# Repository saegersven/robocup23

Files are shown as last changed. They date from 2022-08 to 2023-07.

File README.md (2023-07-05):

# Robocup Junior Rescue Line 2023
### Team BitFlip

* [Youtube Channel](https://www.youtube.com/@evbrobocup)
* [Website](http://kraemer123.de/)
* [2022 Repository](https://github.com/saegersven/robocup)

### <u>Our ToDo List:</u>

#### Software
- [ ] ignore silver for 1s after ramp to get rid of false positives when driving down seesaw/ramp
- [ ] LoPs in rescue area not working
- [ ] check_silver after restart not working, cam servo does not tilt upwards
- [ ] after green dot: check left/right like in Kassel
- [ ] exit
- [ ] investigate: why is cam servo not ALWAYS attached. Sometimes its detached
- [ ] investigate why cam servo sometimes turns when stop.py is being called from run.sh
- [ ] reduce sensitivity when few black pixels (gaps)

#### CAD

#### 3D Printing

### Problems based on runs in St Augustin (descending order of importance, will probably never be implemented)
- [ ] increase motor speed when frame is the same of long time (indicating the robot got stuck)
- [ ] turn lineangle before gap? Maybe drive backwards a few times to allow for slight corrections
- [ ] missed black line during obstacle
- [ ] corner approach: check contour to avoid false positives
- [ ] intersection: confused right with left turn (vid 4, 1:45)
- [ ] obstacle: line after obstacle pls fix
- [ ] prefer living victims when when !ignore_dead 
- [ ] find exit
- [ ] random thread(?) stop during rescue. Maybe add pull down resistor or check for press  duration
- [ ] more labeled victim data to avoid losing victim during search
- [ ] more ml data with multiple victim overlapping (and far away)
- [ ] beginning of victim search: why frame lost?
- [ ] ignore upper frame area when looking for victims
- [ ] find corner more precise (more ml data of corners far away)
- [ ] reajust robot position relative to corner when driving towards it
- [ ] investigate: vid 4, 3:05 random thread crash
- [ ] turn line angle before obstacle
- [ ] check if victim has been rescued successfully (look at black corner)
- [ ] rescue kit: close gripper while driving forward 
- [X] rewrite find_center using VL53L0X and Gyro
- [X] VL53L0X instead of HCSR04
- [X] Gyro sensor (turning, ramps up and down, adjust speed accordingly)
- [X] intersection: turn 60 degs with gyro and rest with camera until line angle = 0
- [X] oscillating during linefollowing (even when following straight lines)
- [X] drive towards rescue kit so its always in the same y position (not only x) to facilitate pickup

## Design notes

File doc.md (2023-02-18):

# Software

Our robot has two programs: The main program runs on a Raspberry Pi 4B+, and is written in C++ with OpenCV and tensorflow as the main dependencies. The secondary program runs on a Teensy 3.6, that acts as a motor controller and receives commands from the main program.

The main program follows the line, navigates intersections, detects obstacles, picks up the rescue kit and rescues the victims using mostly a single Raspberry Pi Camera v2.1 mounted high up at the front of the robot. It is mounted on a servo so it can be rotated upwards to look for victims. During line following, it looks almost straight down.

The main program is written in C++ instead of Python because we perform custom operations on individual pixels, which can't be easily done in Python without significantly sacrificing performance.

## Line following

The main library we use for our Computer Vision tasks is OpenCV. We grab frames from the camera using the library's `cv::VideoCapture` class. We get a `cv::Mat` object which contains a single image. The camera captures in a very low resolution of 80x48 pixels, which combined with optimized algorithms allows the robot to adjust its motor speeds about 100 times per second.

During line following, a frame might look like this:

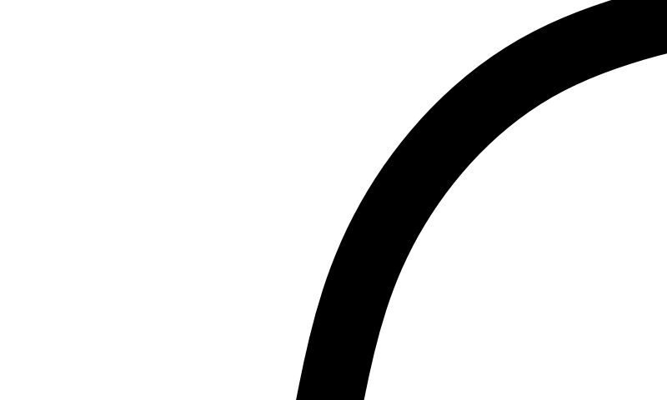
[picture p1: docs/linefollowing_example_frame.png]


Now we use a simple binary thresholding operation to find every black pixel. We now iterate over each of the black pixels and calculate the angle from the bottom center of the image to the pixel:

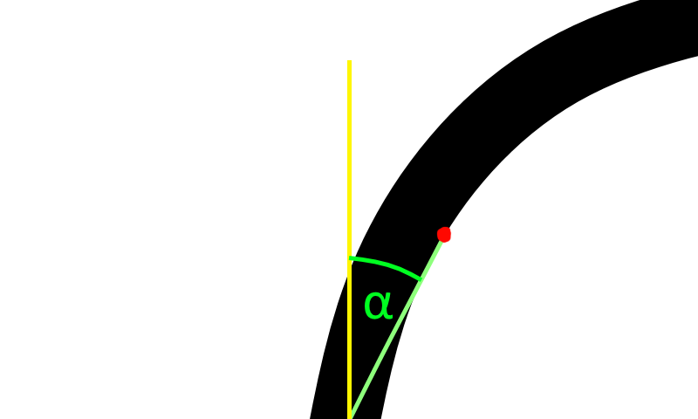
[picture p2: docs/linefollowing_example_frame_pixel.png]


This angle is weighed according to its distance from the bottom center since we don't want pixels near the bottom center to contribute as much to the line angle. Pixels very far away also have lower weights. The pixels are also weighed according to how close their angle is to the angle of the last line. This prevents the robot from following the wrong lines and also helps it navigate T-shaped intersections. The weights are calculated when starting the program and saved in maps for quick access. We now use a weighted average of all the angles of the black pixels to obtain the line angle, which might look like this:

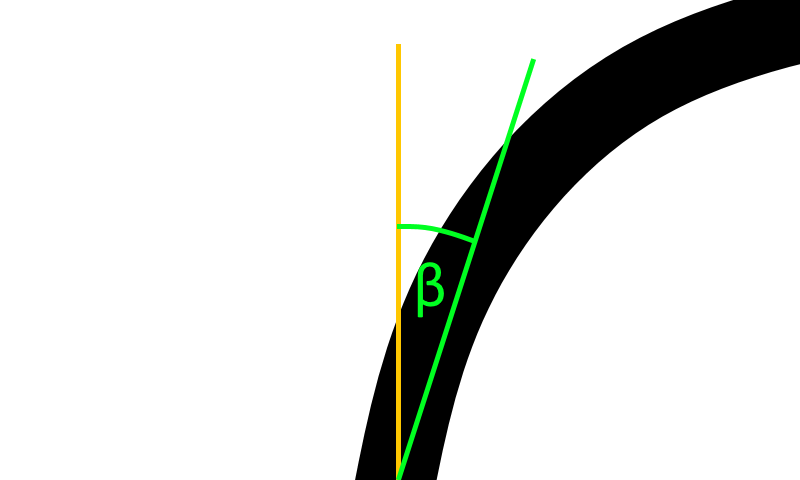
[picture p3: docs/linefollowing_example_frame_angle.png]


This angle is then multiplied by a sensitivity factor and simply added or subtracted from the motor speeds. There is no need for integration or differentiation. This algorithm, combined with a center of rotation of the robot around the front axis, allows the robot to follow even complicated lines very quickly.

### Intersections

During line following, the frame is continuously sampled for green pixels by calculating the ratio of the green component of a pixel to the sum of the blue and red. If there are enough green pixels in the frame, we find contours using a simple recursive algorithm. Contours which are too small are discarded. The only contours that remain are green points.

Now we cut out a square part of the image around the green points and use the binary image from before to iterate over all the black pixels in that cutout. We calculate the average of all the black pixels (depicted below in blue). Now the quadrant of the average black pixel tells us where the robot needs to go. This has proven to be a very simple and robust algorithm.

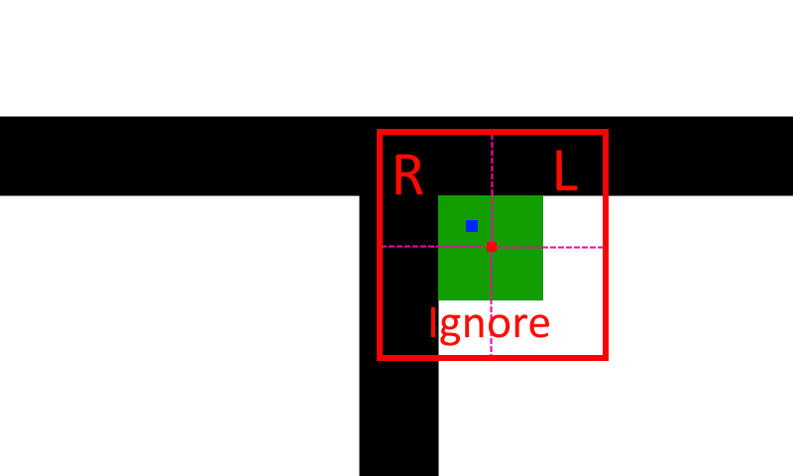
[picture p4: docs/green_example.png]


### Rescue kit

Similarly to the intersection algorithm, we continuously look for blue pixels using the same metric as for green. When we find a contour that is big enough, we calculate the angle from the bottom center to that contour, turn in that direction, pick the rescue kit up and return to following the line.

### Detecting the entrance to the evacuation zone

Detecting a reflecting strip of tape is surprisingly difficult using just a camera. We have tried different algorithms in the past, such as comparing the image to a pre-saved image of the tape, and detecting the reflection of red LEDs mounted near the camera. We now use a small machine learning model trained in Keras/Tensorflow on a few thousand images, which runs simultaneously in a separate thread.

## Evacuation zone

### Strategy

TODO

### Detecting victims

Similarly to the reflective tape at the entrance, two of the victims are reflective as well. This fact as well as debris scattered around the evacuation zone make it difficult to use traditional circle-detection algorithms such as Hough transforms to detect victims. At least we never got it to work reliably. Instead, we are using a machine learning model trained on thousands of images. We have labelled them in Microsoft VoTT. The bounding boxes are assigned one of two tags: "living" or "dead". The neural network is similar to the popular "Yolo" architecture for object detection, but it is greatly simplified.

The image is divided up chunks. For each chunk we want to know if there is a living or a dead victim, or none. This means that the neural net has to essentially output an image with two channels, containing probabilities. Below you can see an input image with 5x4 chunks and two numbers in each chunk, which are probabilities for our two classes "living" and "dead".

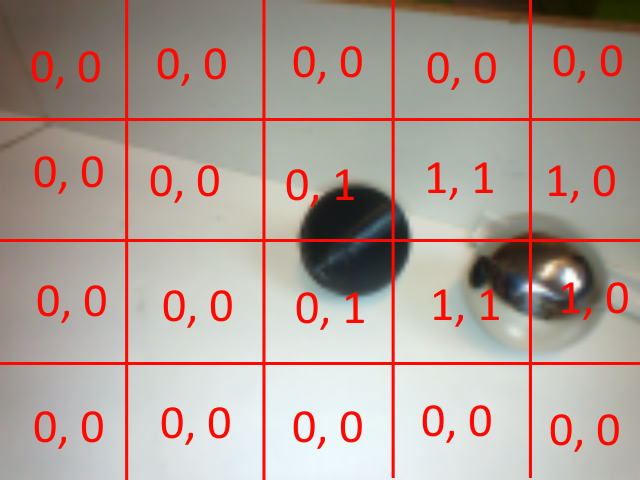
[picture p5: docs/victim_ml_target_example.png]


5x4 chunks is of course not fine enough to pick up victims accurately. We use 32x20 chunks in our model. When visualizing the target images, dead victims appear blue, and living victims green.

The model is created in Python using Keras' `Sequential` class as follows:

```python
model = Sequential([
    layers.Rescaling(1./255, input_shape=(input_height, input_width, 1)),
    layers.Conv2D(8, 5, padding='same', activation='relu'),
    layers.MaxPooling2D(8),
    layers.Conv2D(16, 3, padding='same', activation='relu'),
    layers.Dropout(0.1),
    layers.Flatten(),
    layers.Dense(Ys * Xs * Cs, activation='linear'),
    layers.Reshape((Ys, Xs, Cs))
])
```

Below you can see two training images and their respective targets (left) and two test images on unknown data with output (right).

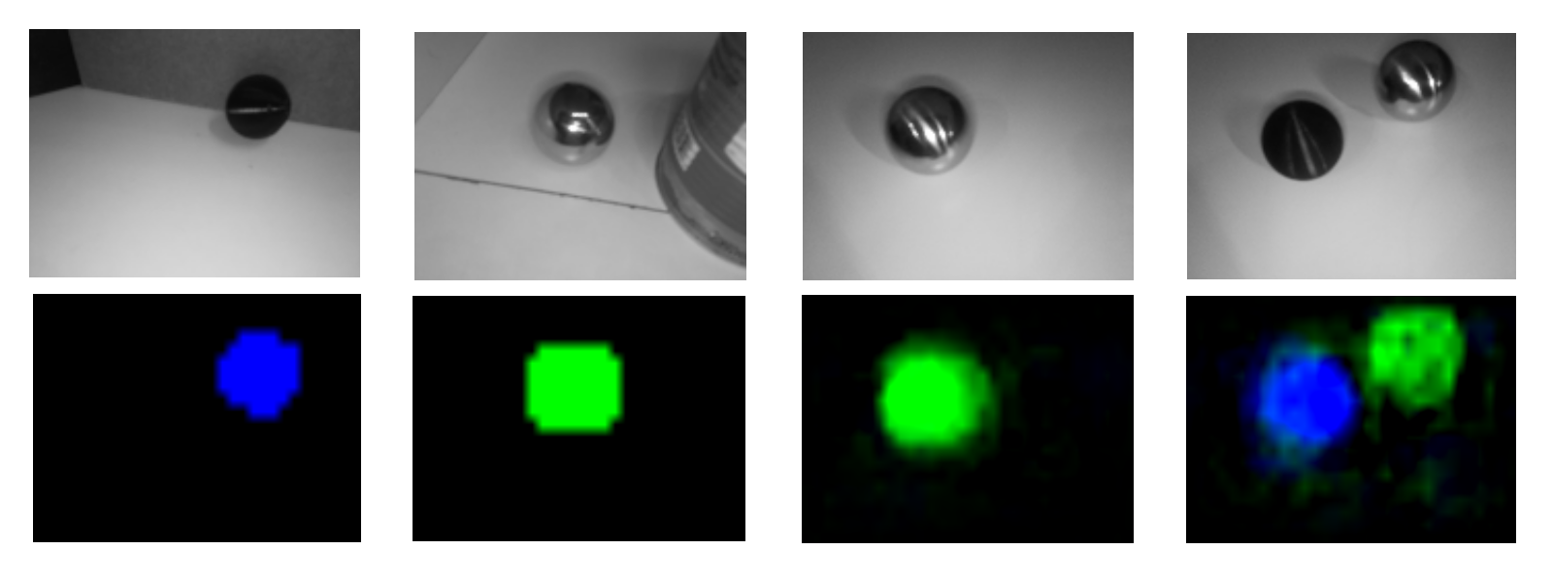
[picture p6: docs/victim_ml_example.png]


Now we just need to extract the victim positions from the output using simple thresholding operations and contour finding. The neural net runs at about 5 fps on the Raspberry Pi and detects victims accurately with almost no false-positives.

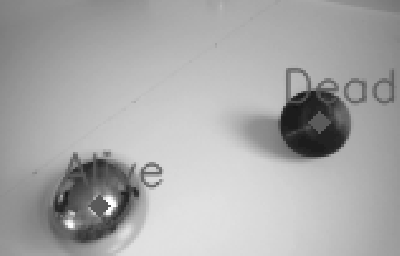
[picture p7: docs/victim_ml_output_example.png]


# Hardware and low-level software

## RasPi <-> Teensy protocol

Communication is via I2C. The Teensy is the secondary device (Address 0x2a) and acts as a motor controller.

| Command | ID | Data | Data type[s] | Description |
| - | - | - | - | - |
| Motor | 11 | Motor speeds | int8[2] | Sets front motor speeds. Rear motor speeds are set automatically |
| Stop | 21 | - | - | Stops all four drive motors |
| Servo | 31 | Servo ID and angle | uint8[2] | Move servo to angle |
| Ready | 41 | - | - | Notify Teensy that the main program is ready to be started |
| Home Servos | 51 | - | - | Set Servos to home positions when resetting the robot |
| Arm Down | 61 | - | - | Move arm down |
| Arm up | 71 | - | - | Move arm up |
| Unload | 91 | - | - | Unload victims and rescue kit |
| Pick up | 101 | - | - | Pick victim up |

Command IDs are non-sequential because communication is very noisy for some reason.

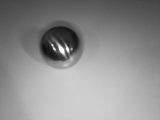
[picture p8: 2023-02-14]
docs/victim_ml_input.png

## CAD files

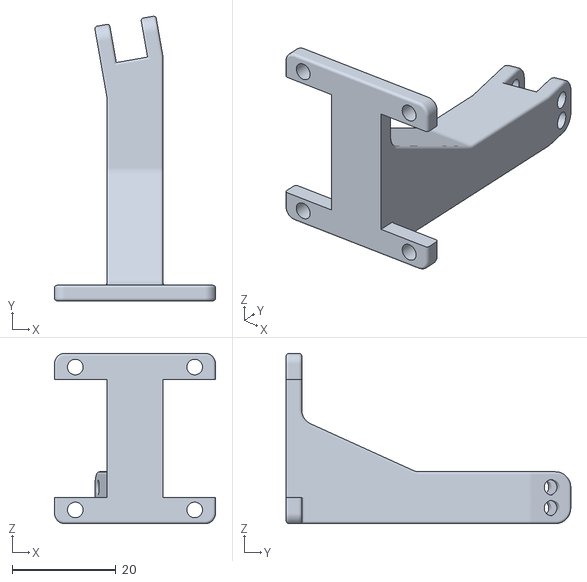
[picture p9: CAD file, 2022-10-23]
files/3D/Greifer_Basis.stl
31.0 x 54.8 x 32.8

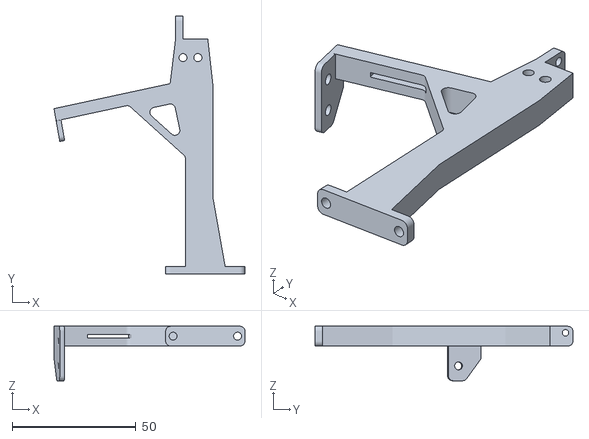
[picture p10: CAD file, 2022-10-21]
files/3D/Camera_Mount.stl
77.0 x 104.0 x 22.0

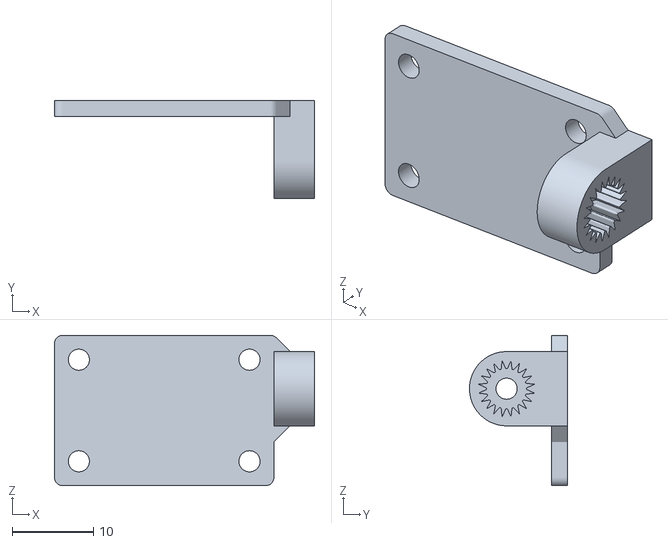
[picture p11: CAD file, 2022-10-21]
files/3D/Camera_Holder.stl
32.0 x 12.1 x 18.5

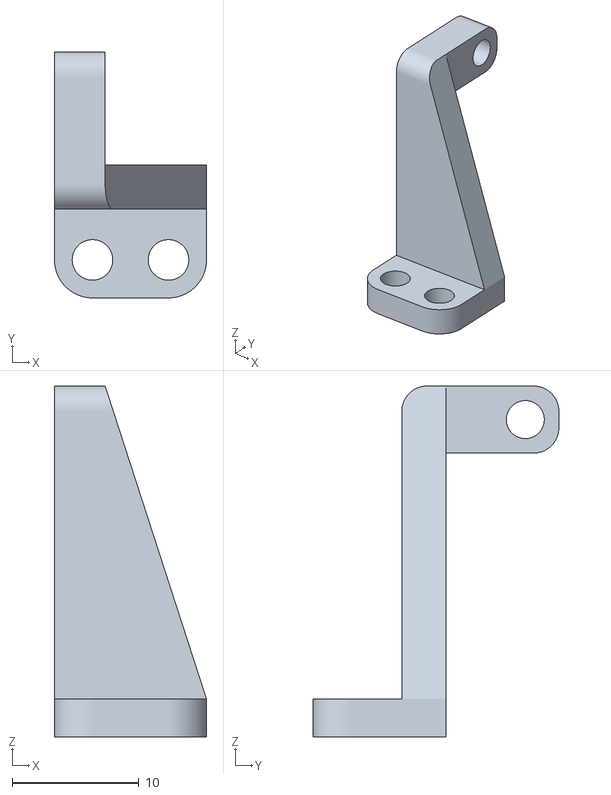
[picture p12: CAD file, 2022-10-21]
files/3D/Camera_Servo_Mount.stl
12.0 x 19.4 x 27.7

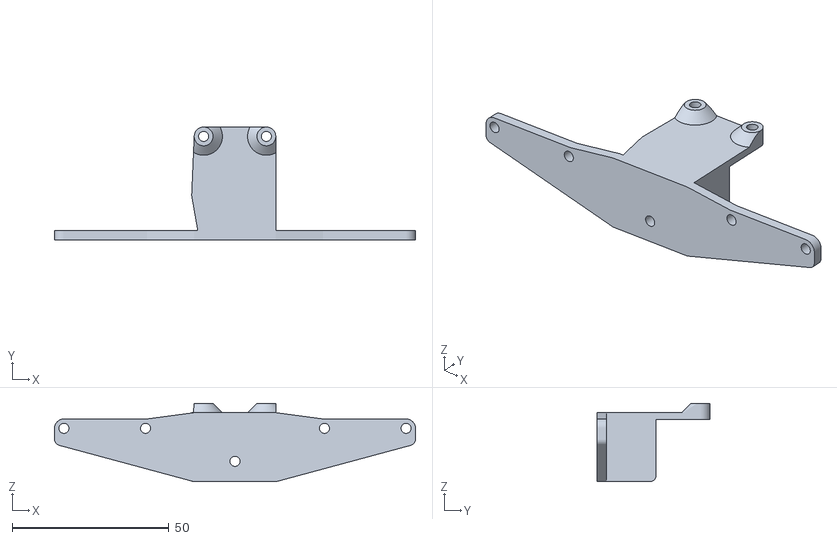
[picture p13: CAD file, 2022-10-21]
files/3D/Front_Mount.stl
115.0 x 36.0 x 25.0

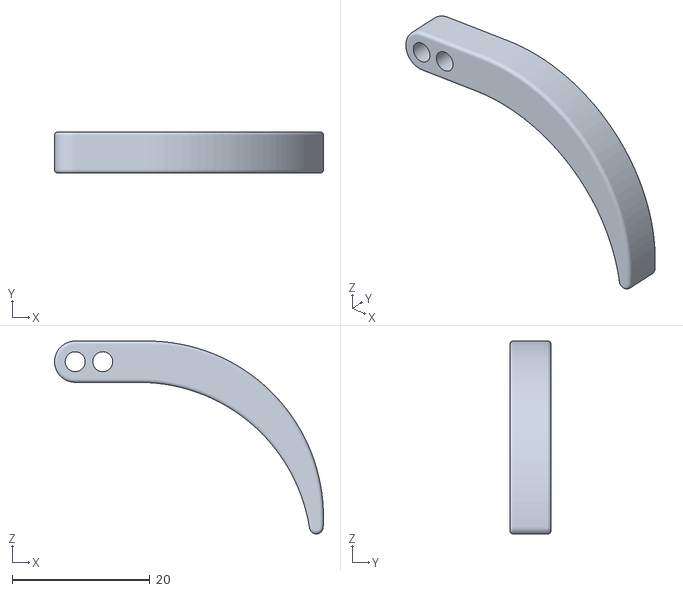
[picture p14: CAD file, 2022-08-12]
files/3D/Greifer_Arm.stl
39.0 x 6.00 x 28.0

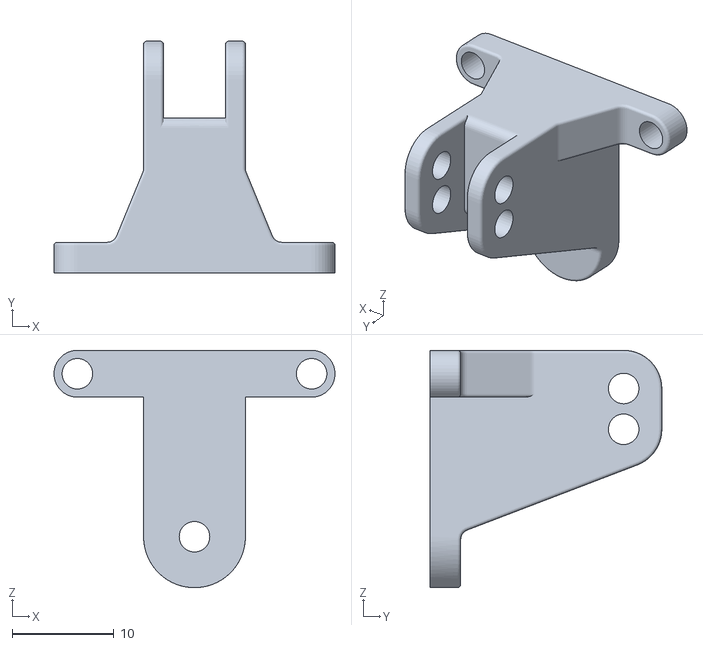
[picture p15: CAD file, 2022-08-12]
files/3D/Greifer_A.stl
27.6 x 22.8 x 23.3

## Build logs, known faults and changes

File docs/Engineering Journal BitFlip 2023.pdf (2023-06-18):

ROBOCUPJUNIOR RESCUE LINE 2023

ENGINEERING JOURNAL

## Team BitFlip

Abstract
This document is mainly about our development process and how we divided the work within our team. Through past RoboCup Junior participations, we gained plenty of experience on how to collaborate efficiently within a team, mainly due to trial and error and constant documenting on what we can improve.
Despite the abstract you are currently reading, this document mainly features a table where we tracked our development process over the past months. To facilitate collaboration, we shared this document through Google Docs with all team members and used a color code to identify areas of responsibility between all team members. The color code is as follows:

Sven Saeger
Jan-Niklas
Lukas
Whole Team

Furthermore, we met on a regular basis, mostly through video calls, however we also made use of GitHub and Trello to manage our todos.

Date | Agenda | Progress/Status | Next steps
July 2022 | | - Selected four 12V DC motors (Pololu 20D) - Researched various servo options and decided to use two servos for arm control and container gate control - Bought according servos - Designed and 3D-printed mounts for the servos and motors | - Complete the design of the robot chassis - Research suitable power source options
Aug ust 2022 | | | | - Assembled chassis with servos and motors - tested various | - Find suitable distance sensor - start PCB design
- Define project requirements and
specifications (new rules?!)
- Research and select components for the robot (mainly actuators)
- Begin designing the robot chassis
- Buy essential parts
- Research: which PCB software is best?
- Test different power source options
- Which sensors are needed?

- Which Microcontroller? | power source options, including: power banks, 2x 18650 and 2S Lipo cells
- Research about
| distance sensors
Sept emb er 2022 | - finished PCB prototype - integration tested motors with chassis and PCB | - start actual PCB design - design
Octo ber 2022 | - finished schematic - tested chassis + motors (ramps, seesaws, speed bumps, debris, point of rotation) | - start PCB routing - research: design architecture for main program
Nov emb er 2022 | - routed and ordered PCB (jlcPCB) - created repo | - test and assemble PCB ASAP - finish hardware (design and print remaining sensor mounts)
Dez emb er 2022 | - soldered and tested PCB - printed and mounted last 3d printed parts | - test robot as a whole (PCB, chassis) - software prototyping
Janu ary 2023 | - wrote and tested linefollowing - tested NN approach for intersections, worked not as well as our algorithm from last year | - improve intersections (use gyroscope to turn, align to intersection before turning) - rescue area - obstacle
Febr uary 2023 | - linefollowing done - worked on silver detection using tensorflow library - bought replacement Raspberry Pi, Teensy Microcontroller, Step up/down modules and motors | - finish rescue area - verify victim NN performance “in the real world” - test under competition conditions
- Intensive integration testing of motors and power supply
- PCB prototyping using perfboard
- create EasyEDA account
- start PCB schematic
- finish PCB
- order PCB
- Research: fast, but affordable PCB manufacturer
- write main routines and functions
- create new github repo
- integration test PCB
- finish hardware
- write linefollowing routine
- test linefollower
- order replacement parts
- finish rescue area
- create ml data for victims
- label ml data
- train victim NN, research about cloud computing
- train silver NN
- finish and test obstacle
- improve intersections (use gyroscope to turn, align to intersection before turning)

| - trained victim NN using google collab to facilitate collaboration within the team
Marc h 2023 | | - wrote packing list - all tests successful | - program exit (after evacuation zone)
- write packing list for German
Opens
- last tests

April
2023
- German Opens | - German Opens | - redesign gripper to use DC motor instead of servo (should work more reliable)
- increase
| | linefollowing speed
- redesign PCB
| | using better step up/down modules and Arduino Nano instead of Teensy as its easier to buy nowadays and more reliable
- decrease overall
| | chassis size
May 2023 | - redesigned gripper to use DC motor - new PCB design - designed new, smaller chassis | - update old 3d files - assemble PCB - test PCB - complete hardware of robot
June 2023 | - finished PCB - redesigned and printed mounts for camera and VL53L0X distance sensors - redesigned and printed BNO055 mount - redesigned victim container - competition simulation - booked hotel - registered team and mentor | - write “packing list” for World Cup - print replacement parts
- redesign gripper to use DC motor
instead of servo (should work more
reliable)
- increase linefollowing speed
- redesign PCB using better step up/down modules and Arduino Nano instead of Teensy as its easier to buy nowadays and more reliable
- decrease overall chassis size
- design new mounts etc due to new chassis
- solder PCB
- intensive testing
- create more ml data for victims
- label new data
- train new model
- World Cup registration and hotel booking
- create Poster about robot
- write TDP

- wrote TDP
- created and
printed poster

Appendix
For further information about our development process, please do not hesitate to check out our GitHub repository:

https://github.com/saegersven/robocup23

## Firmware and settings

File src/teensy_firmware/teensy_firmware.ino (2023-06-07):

#include <Servo.h>
#include <SPI.h>

#include "defines.h"

Servo servo_cam;
Servo servo_arm;
Servo servo_gripper1;
Servo servo_gripper2;
Servo servo_gate;


// GLOBAL VARIABLES
uint8_t buffer[128]; // stores received spi data
uint8_t num_bits = 0; // number of received bits

const Servo servos[5] = {
  servo_cam,
  servo_arm,
  servo_gripper1,
  servo_gripper2,
  servo_gate
};

const int servo_pins[5] = {
  SERVO_CAM_PIN,
  SERVO_ARM_PIN,
  SERVO_GRIPPER1_PIN,
  SERVO_GRIPPER2_PIN,
  SERVO_GATE_PIN
};

#define DEBUG 1
// only print when in debug mode:
#if DEBUG == 1
#define debug(x) Serial.print(x)
#define debugln(x) Serial.println(x)
#else
#define debug(x)
#define debugln(x)
#endif

void setup() {
  init();
}

// interrupt is called on rising spi clock
void sck_rising_interrupt() {
  buffer[num_bits / 8] |= digitalRead(MOSI_PIN) << (7 - num_bits % 8); // write received data to buffer
  ++num_bits;
}

float minvol = 10.0;
void loop() {
  while (digitalRead(CS_PIN) != LOW);
  while (digitalRead(CS_PIN) == LOW);
  int len = num_bits / 8;
  num_bits = 0;

  int cmd = (int)buffer[0]; // received command

  if (cmd == CMD_MOTOR) {
    // [CMD_MOTOR, left, right]
    int8_t left = (int8_t)buffer[1];
    int8_t right = (int8_t)buffer[2];

    m(left, right, 0);

    debug("M: ");
    debug(left);
    debug(" ");
    debugln(right);
  } else if (cmd == CMD_STOP) {
    stop();
  } else if (cmd == CMD_SERVO) {
    // [CMD_SERVO, servo_id, angle]
    uint8_t servo_id = buffer[1];
    uint8_t angle = buffer[2];

    servos[servo_id].attach(servo_pins[servo_id]);
    debug("Attached Servo: ");
    debugln(servo_id);
    servos[servo_id].write(angle);
    debug("Written Angle: ");
    debugln(angle);
    if (servo_id != 0) {
      delay(800); // wait for servo to finish turning
      servos[servo_id].detach(); // detach servo after turning (despite camera servo)
    }

    /*
      debug("S: ");
      debug((int)data[1]);
      debug(" to ");
      debugln((int)data[2]);
    */
  } else if (cmd == CMD_READY) {
    displayBatVoltage();
    digitalWrite(LED3, HIGH);
    delay(30);
    digitalWrite(LED3, LOW);
  } else if (cmd == CMD_SERVOS_HOME_POS) {

    servo_cam.attach(SERVO_CAM_PIN);
    servo_arm.attach(SERVO_ARM_PIN);
    servo_gripper1.attach(SERVO_GRIPPER1_PIN);
    servo_gripper2.attach(SERVO_GRIPPER2_PIN);
    servo_gate.attach(SERVO_GATE_PIN);

    servo_cam.write(CAM_LOWER_POS);
    servo_gripper1.write(GRIPPER1_CLOSED);
    servo_gripper2.write(GRIPPER2_CLOSED);
    servo_arm.write(ARM_HIGHER_POS);
    servo_gate.write(GATE_CLOSED);

    // wait for servos to finish turning
    delay(800);

    //servo_cam.detach(); // cam servo stays attached
    servo_gripper1.detach();
    servo_gripper2.detach();
    servo_arm.detach();
    servo_gate.detach();

  } else if (cmd == CMD_ARM_DOWN) {
    arm_down();
    Serial.println("Received CMD_ARM DOWN");
  } else if (cmd == CMD_ARM_UP) {
    arm_up();
  } else if (cmd == CMD_ARM_HALF_UP) {
    arm_half_up();
  } else if (cmd == CMD_UNLOAD) {
    unload_victims();
  } else if (cmd == CMD_PICK_UP_RESCUE_KIT) {
    pick_up_rescue_kit();
  } else if (cmd == CMD_PICK_UP_VICTIM) {
    pick_up_victim();
  }

  // clear buffer
  for (int i = 0; i < len; ++i) {
    buffer[i] = 0;
  }
}

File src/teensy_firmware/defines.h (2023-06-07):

// general pins
#define LED1 37 // green LED on PCB
#define LED2 38 // red LED on PCB
#define LED3 32 // LED ring from restart btn
#define BAT_VOLTAGE A20

// motors
#define LF1_PIN 3
#define LF2_PIN 4
#define LF_PWM_PIN 2

#define LB1_PIN 9
#define LB2_PIN 8
#define LB_PWM_PIN 10

#define RF1_PIN 16
#define RF2_PIN 17
#define RF_PWM_PIN 14

#define RB1_PIN 6
#define RB2_PIN 5
#define RB_PWM_PIN 7

#define GRIPPER_MOTOR_PIN1 25
#define GRIPPER_MOTOR_PIN2 26

#define BACKWHEEL_FACTOR 1.1 // diameter of front wheels is roughtly 10% greater than diameter of back wheels

// servo pins
#define SERVO_CAM_PIN 21 // servo to change cam position
#define SERVO_GRIPPER1_PIN 0
#define SERVO_GRIPPER2_PIN 0
#define SERVO_ARM_PIN 22 // servo to lift up gripper
#define SERVO_GATE_PIN 23 // servo to empty victim container

// servo position (UPDATE IN BOTH FILES!!!)
#define CAM_LOWER_POS 73
#define CAM_HIGHER_POS 140
#define ARM_LOWER_POS 7
#define ARM_HIGHER_POS 180

#define GATE_OPEN 110
#define GATE_CLOSED 17
#define GRIPPER1_CLOSED 0
#define GRIPPER1_OPEN 0
#define GRIPPER2_CLOSED 0
#define GRIPPER2_OPEN 0

// SPI Pins
#define MISO_PIN 12
#define MOSI_PIN 11
#define SCK_PIN 13
#define CS_PIN 15

// SPI commands (abitrary numbers)
#define CMD_MOTOR 11
#define CMD_STOP 21
#define CMD_SERVO 31
#define CMD_READY 41
#define CMD_SERVOS_HOME_POS 51
#define CMD_ARM_DOWN 61
#define CMD_ARM_UP 71
#define CMD_ARM_HALF_UP 81
#define CMD_UNLOAD 91
#define CMD_PICK_UP_RESCUE_KIT 101
#define CMD_PICK_UP_VICTIM 111

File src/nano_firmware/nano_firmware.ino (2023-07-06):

#include <VL53L0X.h>
#include <Wire.h>
#include <Servo.h>
#include <Adafruit_Sensor.h>
#include <Adafruit_BNO055.h>
#include <EEPROM.h> // only used for debugging


#include "defines.h"

char message[5];
unsigned int message_pos = 0;
bool led_on = false; // global variable to store current debug led state. Led state can be toggled via RasPi

Servo servos[NUM_SERVOS];

VL53L0X dist_sensors[NUM_VL53L0X];
Adafruit_BNO055 bno = Adafruit_BNO055(55, 0x28);

void setup() {
  Serial.begin(115200);
  Wire.begin();

  // Configure pins
  pinMode(LED_BUILTIN, OUTPUT);

  pinMode(M_LEFT_A, OUTPUT);
  pinMode(M_LEFT_B, OUTPUT);
  pinMode(M_LEFT_FRONT_EN, OUTPUT);
  pinMode(M_LEFT_REAR_EN, OUTPUT);

  pinMode(M_RIGHT_A, OUTPUT);
  pinMode(M_RIGHT_B, OUTPUT);
  pinMode(M_RIGHT_FRONT_EN, OUTPUT);
  pinMode(M_RIGHT_REAR_EN, OUTPUT);

  pinMode(M_GRIPPER_A, OUTPUT);
  pinMode(M_GRIPPER_B, OUTPUT);

  // Configure distance sensors
  for (int i = 0; i < NUM_VL53L0X; ++i) {
    pinMode(dist_xshut_pins[i], OUTPUT);
    delay(10);
    digitalWrite(dist_xshut_pins[i], LOW);
  }
  delay(10);

  for (int i = 0; i < NUM_VL53L0X; ++i) {
    digitalWrite(dist_xshut_pins[i], HIGH);
    delay(10);

    if (!dist_sensors[i].init()) error(3);

    dist_sensors[i].setAddress(dist_addresses[i]);
    dist_sensors[i].setMeasurementTimingBudget(20000);
    //dist_sensors[i].startContinuous();
    dist_sensors[i].setTimeout(100);
    delay(10);
  }

  if (!bno.begin()) error(2);

  if (get_battery_voltage() < 6.5) error(1);

  m(0, 0, 0);
}

void loop() {
  // Delete message after 50ms of silence
  long long start_time = millis();
  while (!Serial.available()) {
    if (millis() - start_time > 50) {
      message_pos = 0;
    }
  }

  while (Serial.available() > 0)  {    
    message[message_pos] = Serial.read();
    //i2cDebug(42, message[message_pos]);
    message_pos++;

    if(message[message_pos - 1] == -1) {
      message_pos = 0;
    }
    
    if (message_pos == message_lengths[message[0] - 1]) {
      parse_message();
      message_pos = 0;
    }
  }
}

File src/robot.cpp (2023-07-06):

#include "robot.h"
extern "C" {
#include <fcntl.h>
#include <unistd.h>
#include <sys/ioctl.h>
#include <sys/types.h>
#include <sys/stat.h>
#include <termios.h>
}

#include <cstdlib>
#include <iostream>
#include <chrono>
#include <thread>
#include <fstream>
#include <sstream>
#include <string>

#include <wiringPi.h>

#include "defines.h"
#include "utils.h"

Robot::Robot() : blocked(false), has_frame(false) {
	init_serial();

	/*if(gpioInitialise() < 0) {
		std::cout << "GPIO initialization failed" << std::endl;
	}

	gpioSetMode(PIN_BTN, PI_INPUT);
	gpioSetPullUpDown(PIN_BTN, PI_PUD_OFF);

	//gpioSetMode(4, PI_INPUT);
	//gpioSetPullUpDown(4, PI_PUD_DOWN);*/

	wiringPiSetupGpio();
	pinMode(PIN_BTN, OUTPUT);

	delay(500); // Wait for Nano to boot up
}

Robot::~Robot() {
	// Cleanup GPIO


	// Close serial
	close(serial_fd);
}

void Robot::init_serial() {
	termios options;
	speed_t baud_rate = B115200;

	std::string dev_filename = "/dev/ttyUSB0";
	std::string dev_name = "ttyUSB0";

	int status;

	while((serial_fd = open(dev_filename.c_str(), O_RDWR | O_NOCTTY | O_NDELAY | O_NONBLOCK)) < 0) {
		std::cout << "Could not open Serial." << std::endl;
		std::cout << "Trying USB1..." << std::endl;
		dev_filename = "/dev/ttyUSB1";
		dev_name = "ttyUSB1";
	}

	std::cout << "Opened serial:" << dev_name << std::endl;

	std::stringstream ss;
	ss << "/sys/bus/usb-serial/drivers/ftdi_sio/" << dev_name << "/latency_timer";
	std::string latency_file_name = ss.str();
	std::cout << "Set latency to 2ms in " << latency_file_name << std::endl;

	std::ofstream out(latency_file_name);
	out << "2" << std::endl;
	out.close();


	fcntl(serial_fd, F_SETFL, O_RDWR);

	tcgetattr(serial_fd, &options);

	cfmakeraw(&options);
	cfsetispeed(&options, baud_rate);
	cfsetospeed(&options, baud_rate);

	options.c_cflag |= (CLOCAL | CREAD);
	options.c_cflag &= ~PARENB;
	options.c_cflag &= ~CSTOPB;
	options.c_cflag &= ~CSIZE;
	options.c_cflag |= CS8;
	options.c_lflag &= ~(ICANON | ECHO | ECHOE | ISIG);
	options.c_oflag &= ~OPOST;

	options.c_cc[VMIN] = 0;
	options.c_cc[VTIME] = 5; // 0.5 seconds (5 deciseconds)

	tcsetattr(serial_fd, TCSANOW, &options);
	ioctl(serial_fd, TIOCMGET, &status);

	status |= TIOCM_DTR;
	status |= TIOCM_RTS;

	ioctl(serial_fd, TIOCMSET, &status);

	delay(10);
}

void Robot::start_camera() {
	cap.open(0, cv::CAP_V4L2);
	cap.set(cv::CAP_PROP_FRAME_WIDTH, capture_width);
	cap.set(cv::CAP_PROP_FRAME_HEIGHT, capture_height);
	cap.set(cv::CAP_PROP_FORMAT, CV_8UC3);
	cap.set(cv::CAP_PROP_FPS, 60);

	if(!cap.isOpened()) {
		std::cout << "Could not open camera." << std::endl;
		exit(ERRCODE_CAM_SETUP);
	}

	camera_running = true;
	has_frame = false;

	std::thread t([this] {this->camera_thread();});
	t.detach();
}
// constantly grabs frame from camera
void Robot::camera_thread() {
	//auto time = std::chrono::high_resolution_clock::now();
	while(camera_running) {
		//auto now_t = std::chrono::high_resolution_clock::now();
		//long long dt = std::chrono::duration_cast<std::chrono::microseconds>(now_t - time).count();
		//std::cout << 1000000.0f / (float)dt << std::endl;
		//time = now_t;
		cap.grab();
		frame_lock.lock();
		cap.retrieve(curr_frame);
		cv::resize(curr_frame, curr_frame, cv::Size(frame_width, frame_height));
		frame_lock.unlock();
		has_frame = true;
	}
}

void Robot::stop_camera() {
	cap.release();
	camera_running = false;
	has_frame = false;
}

cv::Mat Robot::grab_frame() {
	if(!camera_running) std::cout << "Grabbing frame with closed camera" << std::endl;

	while(!has_frame);
	
	frame_lock.lock();
	has_frame = false;

	cv::Mat frame;
	cv::flip(curr_frame, frame, -1);
	frame_lock.unlock();

	return frame;
}

void Robot::set_cam_angle(uint8_t angle) {
	int pw = (int)(((float)angle / 180.0f + 1.0f) / 0.1f * 1024.0f);
	std::cout << "Pulse width: " << pw << std::endl;
	if(pw < 0) pw = 0;
	if(pw > 1024) pw = 1024;
	//pwmWrite(SERVO_CAM_PIN, pw);
}

void Robot::set_blocked(bool blocked) {
	this->blocked = blocked;
}

int Robot::serial_available() {
	int res;
	if(ioctl(serial_fd, FIONREAD, &res) == -1) return -1;

	return res;
}

bool Robot::button() {
    /*bool reading = gpioRead(PIN_BTN); // Read the state of the button

    if (reading != lastButtonState) {
        lastDebounceTime = millis_(); // Reset the debounce timer
    }

    if ((millis_() - lastDebounceTime) > 50) { // change 50ms if needed
        if (reading != buttonState) {
            buttonState = reading;
        }
    }

    lastButtonState = reading;*/
    //return false;
    for(int i = 0; i < 4; i++) {
    	if(!digitalRead(PIN_BTN)) {
    		return false;
    	}
    }

    return true;
}

void Robot::m(int8_t left, int8_t right, int32_t duration) {
	//std::cout << "left: " << static_cast<int>(left) << "  right: " << static_cast<int>(right) << "  dur: " << duration << std::endl;
	if(blocked) return;
	if(duration < 0) {
		duration = -duration;
		left = -left;
		right = -right;
	}
	if(duration > 65535) duration = 65535;
	uint16_t dur = duration;

	// -1 is sync byte
	if(left == -1) left = 0;
	if(right == -1) right = 0;

	char msg[6] = {0xFF, CMD_MOTOR, *((char*)&left), *((char*)&right), 0, 0};
	memcpy(&msg[4], &dur, 2);

	tcflush(serial_fd, TCIFLUSH);

	write(serial_fd, msg, 6);
	delay(duration);
}

void Robot::stop() {
	if(blocked) return;

	char msg[2] = {0xFF, CMD_STOP};
	write(serial_fd, msg, 2);
}

void Robot::send_ready() {
	char msg = CMD_READY;
	write(serial_fd, &msg, 1);

	tcflush(serial_fd, TCIFLUSH);
}

// turns given angle in radians
void Robot::turn(float angle) {
	if(blocked) return;

	std::cout << "Turning Angle: " << RTOD(angle) << std::endl;

	if(std::abs(RTOD(angle)) < 30.0f) {
		float sign = angle / std::abs(angle);
		int dur = (int)(RTOD(std::abs(angle)) * MS_PER_DEGREE);
    	m(sign * 50, -sign * 50, dur);
		return;
	}
	
	int16_t angle_mrad = angle * 1000;
	char msg[4] = {0xFF, CMD_TURN, 0, 0};
	memcpy(&msg[2], &angle_mrad, 2);

	write(serial_fd, msg, 4);

	tcflush(serial_fd, TCIFLUSH);

	uint64_t start_t = millis_();

	// wait until turn is finished. Currently not working @saegersven
	while (1) {
		char msg[1] = {0};
		read(serial_fd, &msg, 1);
		std::cout << msg[0] << std::endl;
		if (CMD_TURN_DONE == msg[0]) {
			//std::cout << "Received done, msg is: " << (int)msg[0] << std::endl;
			break;
		}
		if(start_t - millis_() > 6000) break;
	}

	tcflush(serial_fd, TCIFLUSH);
}

void Robot::attach_detach_servo(uint8_t servo_id) {
	if(blocked) return;

	uint8_t msg[3] = {0xFF, CMD_SERVO_ATTACH_DETACH, servo_id};

	write(serial_fd, msg, 3);
}

void Robot::servo(uint8_t servo_id, uint8_t angle, uint16_t delay_ms) {
	if(blocked) return;

	uint8_t msg[4] = {0xFF, CMD_SERVO_WRITE, servo_id, angle};
	write(serial_fd, msg, 4);
	if(delay_ms != 0) delay(delay_ms);
}
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

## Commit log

2022-08-12 Added arm STLs
    [Greifer_A.stl, Greifer_Arm.stl, Greifer_Basis.stl]
2022-08-28 added pcb files
    [Greifer_A.stl, Greifer_Arm.stl, Greifer_Basis.stl]
2022-09-18 battery indicator test
2022-09-19 proper battery indicator
2022-09-21 added proper lipo voltage values
2022-09-21 Added untested SPI test
2022-10-07 Added back wheel speed formula
2022-10-08 Added chassis drawing
2022-10-21 Added STLs
    [Camera_Holder.stl, Camera_Mount.stl, Camera_Servo_Mount.stl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]
2022-10-21 spi debugging
2022-10-23 working i2c test
2022-10-23 Added Arm base
    [Greifer_Basis.stl]
2022-10-24 added function for controlling (single) motors
2022-11-02 working motor test
2022-11-02 working servo test
2022-11-04 Linefollowing, teensy side
2022-11-04 added pcb schematic
2022-11-07 added LED3 functionality
2022-11-07 added CMD_START in Teensy firmware, TODO: add in RasPi program
2022-11-07 fixed wrong CMD_START in Teensy firmware
    [defines.h]
2022-11-12 added and tested servo pins and values
2022-11-16 Updated I2C Protocol in doc.md
2022-11-20 gyro testing
2022-12-02 Implemented VL53L0X and Pi-side servo control
2022-12-10 Fixed silver and added temporary test
    [line.cpp, line.h]
2022-12-10 working silver NN, fixed save_img
    [line.cpp, main.cpp]
2022-12-10 i2c tests, not working
    [functions.ino, line.cpp, main.cpp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]
2022-12-11 spi tests, not working
    [main.cpp, pi_spi_test.cpp, robot.h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]
2022-12-12 working spi test, still some bugs
    [pi_spi_test.cpp, teensy_spi_test.ino]
2022-12-13 working spi test
2022-12-13 SPI Pi implementation
2022-12-13 implemented spi in main program
2022-12-14 fixed spi communication, worked on intersections
    [line.cpp, line.h, main.cpp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]
2022-12-15 controlling servos via raspi, fixed debug led
    [functions.ino, main.cpp, robot.h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]
2022-12-15 automatic return to servo home position after restart
2022-12-23 pick up victim, servo test
2023-01-02 initing camera in rescue!
2023-01-04 saves frame when detecting silver
2023-01-07 obstacle motor values
2023-02-16 adjusted servo positions
2023-02-19 autostart und stuff list§
2023-03-16 new gripper
2023-04-09 comment out gap correction, TODO: fix
    [line.cpp]
2023-04-12 increase motor speed when stuck
    [line.cpp, line.h]
2023-05-11 added new PCB gerber file
2023-05-13 Started writing new nano firmware. Distance sensors and servos done
2023-05-16 Implemented more of Nano firmware. New Camera in line
2023-05-22 motor test
2023-05-23 Nano firmware, turn, fixed m, variable message lengths
    [defines.h, functions.ino, nano_firmware.ino]
2023-05-29 USB tests, not working
    [functions.ino, line.cpp, main.cpp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]
2023-05-29 Serial latency timer, may be fixed now
    [robot.cpp]
2023-06-05 status led, servo
2023-06-09 dist sensor tests
2023-06-09 dist sensor
2023-06-09 gyro: heading and pitch
2023-06-10 worked on servo. Not working
    [main.cpp, robot.cpp, robot.h]
2023-06-13 set servos to home pos
2023-06-14 fixed random stops at startup
    [defines.h, functions.ino, main.cpp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]
2023-06-14 investigated freezes, probably caused by robot->turn and robot->servo commands
2023-06-20 fixed hardware bugs, front and rear motors turn equal now
    [functions.ino, main.cpp, nano_firmware.ino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]
2023-06-21 bug fixes, still not working
    [line.cpp, main.cpp, robot.cpp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]
2023-06-21 fixed errors in corner_ml.cpp
    [line.cpp, rescue.cpp, robot.cpp]
2023-06-22 CMD_READY, button and turn still not working
    [defines.h, functions.ino, main.cpp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]
2023-06-23 button and distance
2023-06-26 bug fixes, button
2023-06-28 button debouncing
2023-06-28 resolved crooked driving, hardware problem
    [functions.ino, line.cpp, main.cpp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]
2023-06-30 i2c debugging
2023-06-30 USB fix, somewhat working
    [functions.ino, line.cpp, main.cpp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]
2023-07-06 quick fix for usb problems
    [line.cpp, main.cpp, rescue.cpp]
2023-07-06 0xFF for servo commands
